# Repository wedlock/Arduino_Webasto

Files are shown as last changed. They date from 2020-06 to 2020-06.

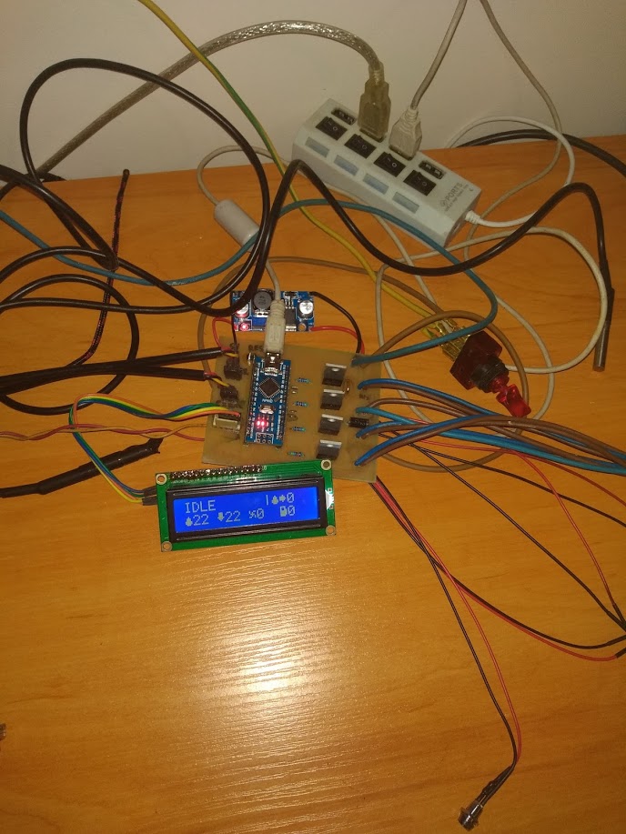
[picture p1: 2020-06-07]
IMG_20200114_202123214.jpg

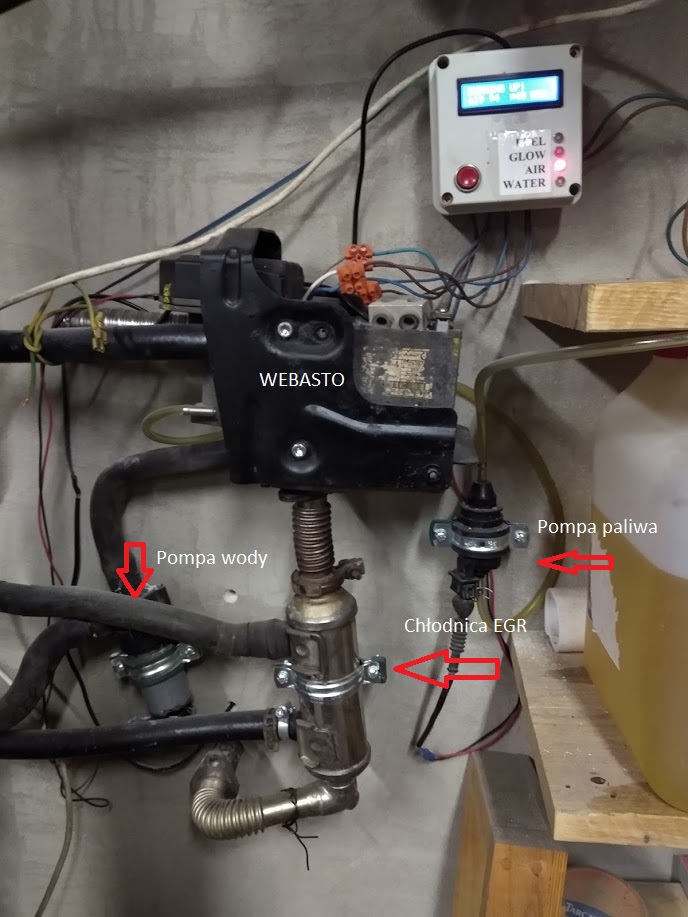
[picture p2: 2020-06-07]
IMG_20200213_185957531.jpg

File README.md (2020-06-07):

# Arduino_Webasto

Projekt sterownika do Webasto oparty na adruino ( w tym przyopadku Adruino nano ). Do działania całości niezbędne są dwa termometry ( DS18B20 ) do odczytu temperatury spalin i cieczy w układzie oraz wyświetlacz LCD 2x16 linii , 1 przycisk monostabilny, kilka rezystorów, MOSFETY i diody LED  ( wszystkie elementy są wymienione w schemacie ). Sterownik ustawiony jest na maksymalną temperaturę 70 stopni .

Do projektu dołączam pliki EAGLE i PDF niezbędne do wykonania płytki.

Krótka instrukcja działania :

Gdy sterownik znajduje się w stanie IDLE jednoktorne wciśnięcie przycisku powoduje rozpoczęcie sekwencji startowej. Na ekranie wyświetla się napis BURNING UP. Ponowne wciśnięcie przycisku w każdym momencie gdy sterownik jest w trybie BURNING UP, WORKING albo SLEEP powoduje wygaszenie pieca. Przytrzymanie przycisku 2 sek powoduje natychmiastowe zatrzymanie i reset programu.

Podczas pracy sterownik cały czas sprawdza temp. spalin i wody i gdy wykryje nieprawidłowości wyłącza układ. Mi osobiście przez całą zimę nie wyłączył się awaryjnie ani razu. Dla bezpieczeństwa wbudowałem watchdoga, który co kilka milisekund sprawdza czy arduino się zawiesiło, a jeśli tak to resetuje cału układ i wygasza się on bezpiecznie.

Stany sterownika:
1. IDLE oczekuje na włączenie ( sprawdzanie temp. cieczy ciągle włączone i ewentualnie włączy się pompa wody gdy temperatura wzrośnie )
2. BURNING UP rozpalanie pieca. Odbywa się to etapami :
  - przedmuchanie komory spalania celem pozbycia się oparów ropy
  - którkie pomowanie paliwa żeby rozsączyło się na palniku i odczekanie kulku sekund
  - włączenie świecy żarowej
  - gdy nastąpi wzrost temp. wody o 3 stopnie lub temp. wody o 2 stopnie piec przechodzi w tryb działania WORK
3. WORK - normalna praca pieca. Przy temp wody 20 stopni pompa wody jest włączana na 1/2 mocy. Zapobiega to gotowaniu się wody na powierzchni webasta. Po ogrzaniu się wody do 30 stopni sterownik urychamia się na 100% mocy. Gdy temp wody dojdzie do 70 stopni piec usypia się i czeka aż woda ostygnie do 65 stopni po czym znowy się uruchamia
4. BURN OFF wygaszanmie pieca. Nie jest podawane paliwa a wiatrak zwalnia. Zapobiega to cofaniu się płomienia. Gdy temp. spalin i wody przez dłuższą chwilę nie wzrasta, piec wyłącza się.

Na płytce zapomniałem dodać pinów do wlutowania przycisku ( ups. ) ale bez problemu da się to przylutować bezpośrednio do płytki. Są to przewody sygnałowe i ich średnica może być nawet i 0,5mm

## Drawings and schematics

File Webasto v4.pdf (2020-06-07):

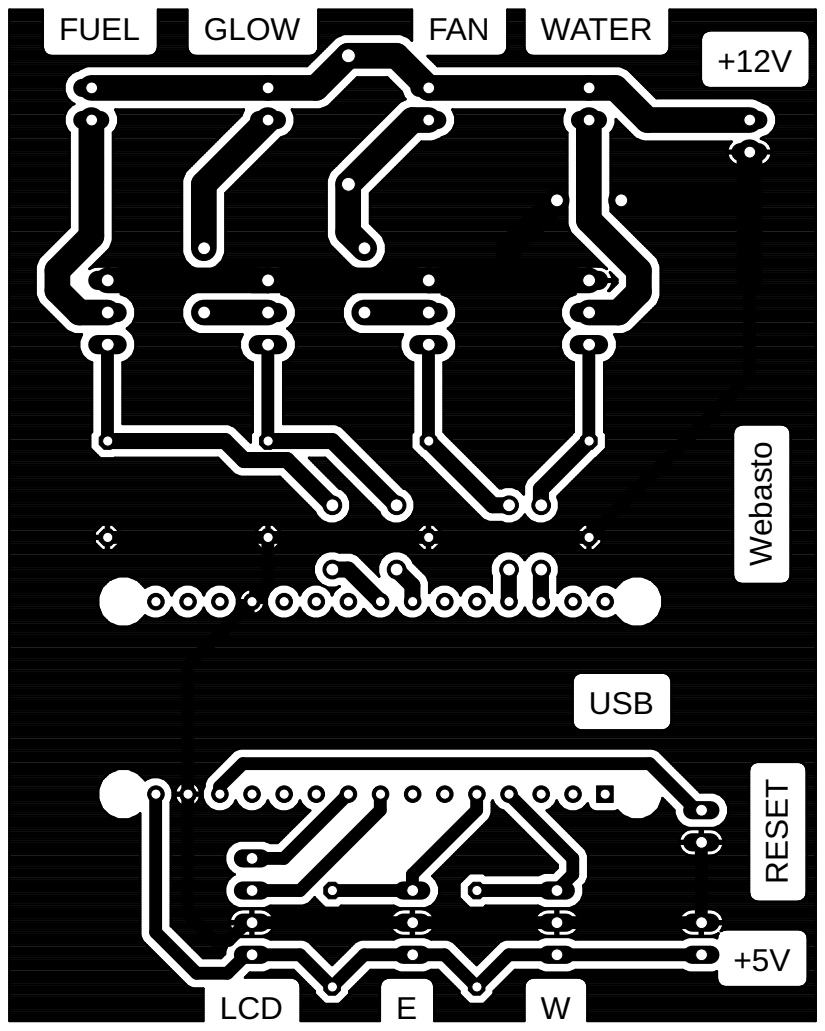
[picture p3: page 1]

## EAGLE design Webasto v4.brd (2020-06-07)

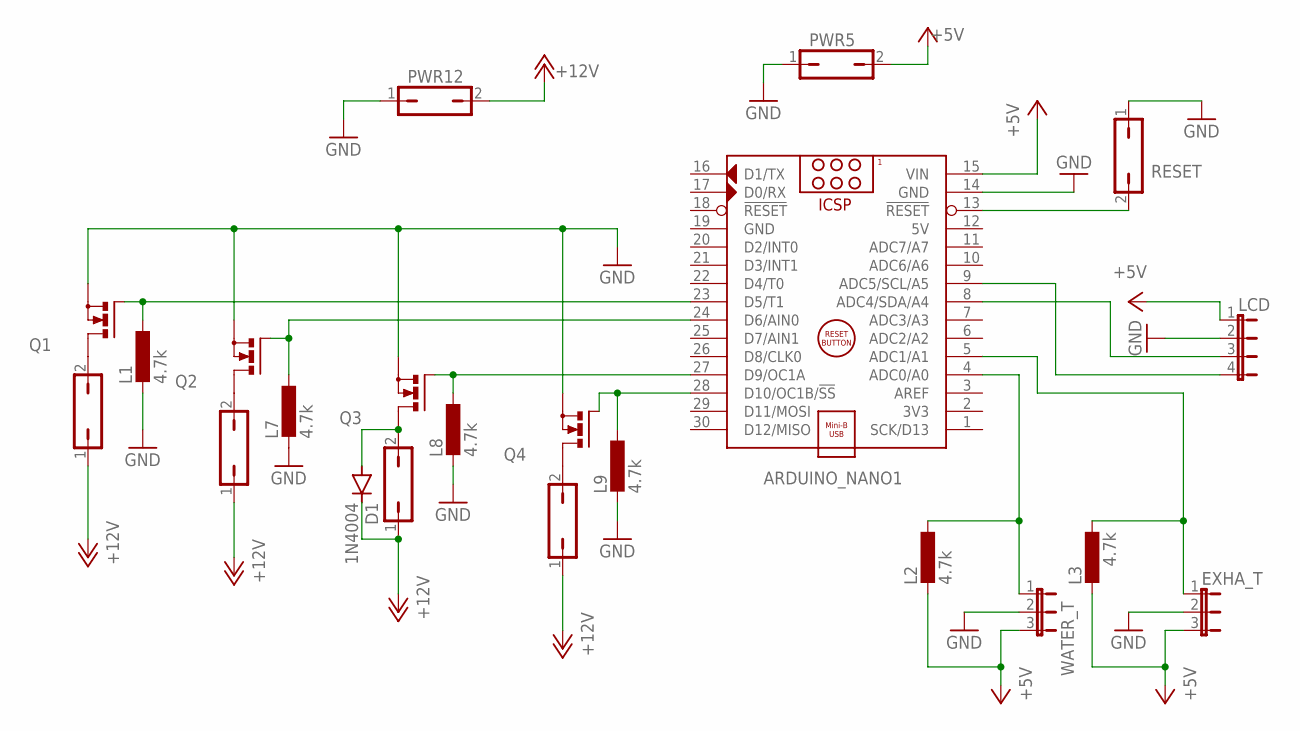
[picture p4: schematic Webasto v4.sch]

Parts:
ARDUINO_NANO1: ARDUINO_NANO
D1: 1N4004; DO41-10
EXHA_T: JP2E; JP2
FAN: 794681-2; JP1
FUEL: 794681-2; JP1
GLOW: 794681-2; JP1
L1, L2, L3, L7, L8, L9: 4.7k; 0204/7
LCD: JP4E; JP4
PWR5, PWR12: JP1Q; JP1
Q1, Q2, Q3, Q4: IRLB8721; TO220BV
RESET: power; JP1
WATER: 794681-2; JP1
WATER_T: JP2E; JP2

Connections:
5V: ARDUINO_NANO1.12 (5V)
+5V: ARDUINO_NANO1.15 (VIN), EXHA_T.3, L2.2, L3.2, LCD.1, PWR5.2, WATER_T.3
+12V: D1.C, FAN.1, FUEL.1, GLOW.1, PWR12.2, WATER.1
GND: ARDUINO_NANO1.14 (GND), ARDUINO_NANO1.19 (GND), EXHA_T.2, L1.2, L7.2, L8.2, L9.2, LCD.2, PWR5.1, PWR12.1, Q1.S, Q2.S, Q3.S, Q4.S, RESET.1, WATER_T.2
unnamed: ARDUINO_NANO1.23 (D5/T1), L1.1, Q1.G
unnamed: FUEL.2, Q1.D
unnamed: ARDUINO_NANO1.24 (D6/AIN0), L7.1, Q2.G
unnamed: GLOW.2, Q2.D
unnamed: ARDUINO_NANO1.27 (D9/OC1A), L8.1, Q3.G
unnamed: D1.A, FAN.2, Q3.D
unnamed: ARDUINO_NANO1.28 (D10/OC1B/!SS), L9.1, Q4.G
unnamed: Q4.D, WATER.2
unnamed: ARDUINO_NANO1.8 (ADC4/SDA/A4), LCD.3
unnamed: ARDUINO_NANO1.9 (ADC5/SCL/A5), LCD.4
unnamed: ARDUINO_NANO1.5 (ADC1/A1), EXHA_T.1, L3.1
unnamed: ARDUINO_NANO1.4 (ADC0/A0), L2.1, WATER_T.1
RESET: ARDUINO_NANO1.13 (!RESET), RESET.2

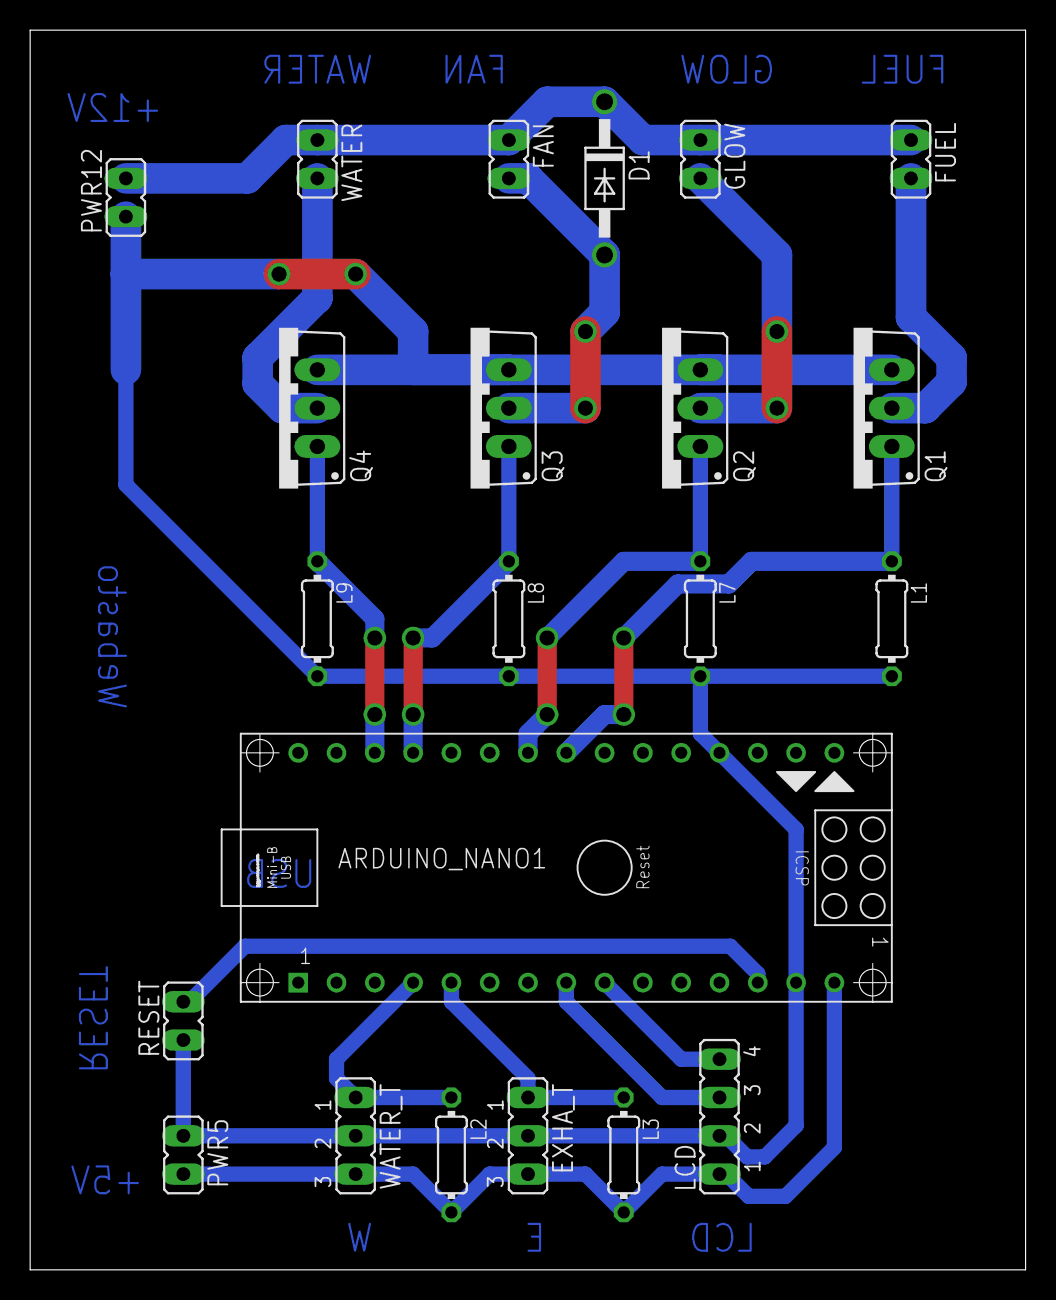
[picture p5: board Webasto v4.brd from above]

Board: 2 copper layers, 66.0 x 82.2 mm, 22 parts (0 on the bottom side), 16 nets.

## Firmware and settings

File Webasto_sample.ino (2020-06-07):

#include "Arduino.h"
#include <math.h> // needed to perform some calculations
#include <Wire.h>
#include <LiquidCrystal_I2C.h>
#include <OneWire.h>
#include <DallasTemperature.h>
#include <avr/wdt.h>

byte fanChar[ ] = {
B00000,
B10011,
B10100,
B01110,
B00101,
B11001,
B00000,
B00000 };
byte fuelChar[ ] = {
B11110,
B10010,
B10011,
B11111,
B11111,
B11111,
B11110,
B00000 };
byte waterChar[ ] = {
B00000,
B00100,
B01110,
B01110,
B11111,
B11111,
B01110,
B00000 };
byte exhaustChar[ ] = {
B01110,
B01110,
B01110,
B11111,
B01110,
B00100,
B00000,
B00000 };
byte w_pumpChar[ ] = {
B00000,
B00100,
B11110,
B11111,
B11110,
B00100,
B00000,
B00000 };

int fuel_pump_pin = 5;
int glow_plug_pin = 6;
int burn_fan_pin = 9;
int water_pump_pin = 10;
//int water_temp_pin = A0;
//int exhaust_temp_pin = A1;
int water_input_index = 0;
int exhaust_input_index = 1;
int button_pin = 3;

int temperature_target = 70;  // degres C
int run_pump_min = 30;  // minimal temperature for run water pump
int fan_speed;  // percent
int water_pump_speed;  // percent
int fuel_need;  // percent
int glow_time;  // seconds
int water_temp;  // degres C
int water_temp_sec[10];
int exhaust_temp;  // degres C
int exhaust_temp_sec[10];  // array of last 10 sec water temp, degres C
int shower_timeout;
int percent_map = 0;
int ignit_fail;
int seconds;

bool shower;
bool burn;
bool webasto_fail;
bool lean_burn;
bool overheating;
int burn_mode = 0;
bool check_pause;

int old_water_temp;
int old_exhaust_temp;
int old_fan_speed;
int old_fuel_need;
int old_fan;

int blink_LED = 13;
int blink_LED_status = 0;

LiquidCrystal_I2C lcd(0x3f, 16, 2);
DeviceAddress deviceAddress;
OneWire ds18x20[ ] = { A0, A1 };
const int oneWireCount = sizeof(ds18x20) / sizeof(OneWire);
DallasTemperature sensor[oneWireCount];

void setup() {
	webasto_fail = false;
	for (int i = 0; i < oneWireCount; i++) {
		sensor[i].setOneWire(&ds18x20[i]);
		sensor[i].begin();
		if (sensor[i].getAddress(deviceAddress, 0))
		    sensor[i].setResolution(deviceAddress, 9);
	}

//	lcd.createChar(0, waterChar);
//	lcd.createChar(1, exhaustChar);
//	lcd.createChar(2, fanChar);
//	lcd.createChar(3, fuelChar);
//	lcd.createChar(3, w_pumpChar);

	TCCR1B = (TCCR1B & 0b11111000) | 0x01;  // magic Fast PWM parameter

	pinMode(glow_plug_pin, OUTPUT);
	pinMode(fuel_pump_pin, OUTPUT);
	pinMode(burn_fan_pin, OUTPUT);
	pinMode(water_pump_pin, OUTPUT);
//	pinMode(water_temp_pin, INPUT);
//	pinMode(exhaust_temp_pin, INPUT);
	pinMode(button_pin, INPUT_PULLUP);  // important, this pulls de button pin to high, so when pressed it goes to low
	pinMode(blink_LED, OUTPUT);

	lcd.init();

	lcd.home();

	lcd.setCursor(0, 0);

	lcd.backlight();
	lcd.createChar(0, waterChar);
	lcd.createChar(1, exhaustChar);
	lcd.createChar(2, fanChar);
	lcd.createChar(3, fuelChar);
	lcd.createChar(4, w_pumpChar);

	check_pause = false;
	overheating = false;

	Serial.begin(9600);
}

void temp_data() {  // keeps the temp variables updated
	static unsigned long timer;
//	if (millis() < timer) {
//		timer = millis();
//	}
// call the get_temp function and smoothen the result
//	water_temp = (9 * water_temp + get_temp(water_temp_pin)) / 10;
//	exhaust_temp = (9 * exhaust_temp + get_temp(exhaust_temp_pin)) / 10;
	water_temp = get_temp(water_input_index);
	exhaust_temp = get_temp(exhaust_input_index);

	if (millis() > timer + 1000) {  // every sec
		timer = millis();

		for (int i = 9; i >= 1; i--) {  // updating the exhaust temperature history
			exhaust_temp_sec[i] = exhaust_temp_sec[i - 1];
			water_temp_sec[i] = water_temp_sec[i - 1];
		}
		exhaust_temp_sec[0] = exhaust_temp;  // add new temp value
		water_temp_sec[0] = water_temp;
	}
}

void control() {
	static unsigned long timer;
	if (millis() < timer) {
		timer = millis();
	}
	static bool pushed;
	static bool long_press;
	bool push;

	if (digitalRead(button_pin)) {
		push = true;
	} else {
		push = false;
	}

	if (!push && !pushed) {
		timer = millis();

	}

	if (push && !pushed) {
		timer = millis();
		pushed = true;
	}

	if (push && pushed && millis() > timer + 500) {
		if (!long_press) {  // when long press
			long_press = true;
			if (webasto_fail) {  // reset webasto fail if there has been a failure
				lcd.setCursor(0, 0);
				lcd.print("RESET     |");
				shower_timeout = 0;
				burn_mode = 0;
				burn = 0;
				glow_time = 0;
				shower = false;
				webasto_fail = false;
				check_pause = false;
				overheating = false;
			}
			if (!webasto_fail && burn_mode > 0) {  // fast stop
				lcd.setCursor(0, 0);
				lcd.print("FAST STOP |");
				burn_mode = 0;
				shower_timeout = 0;
				webasto_fail = false;
				shower = false;
				burn_mode = 0;
				burn = 0;
				glow_time = 0;
				check_pause = false;
				overheating = false;
			}
		}
	}

	if (pushed && !push) {  // if shower is off, turn it on with a 60 seconds timeout
		if (millis() > timer + 50 && !long_press) {  // when short press
			if (burn_mode > 0) {  // if shower is on, turn it off with a 15 second timeout
				lcd.setCursor(0, 0);
				lcd.print("TURN OFF  |");
				shower_timeout = 15;
				shower = false;
				burn_mode = 3;
				burn = 0;
				glow_time = 0;
				seconds = 0;
				check_pause = false;
				overheating = false;
			}
			if (burn_mode == 0) {
				lcd.setCursor(0, 0);
				lcd.print("START     |");
				shower = 1;
				shower_timeout = 99;
				check_pause = false;
				overheating = false;
			}
		}
		pushed = 0;
		long_press = 0;
	}
}

void shower_void() {

	static unsigned long secs_timer;
	if (millis() < secs_timer) {
		secs_timer = millis();
	}

	if (shower) {
		burn = 1;
		if (shower_timeout == 99) {
			shower_timeout = 60;
		}
		if (shower_timeout < 15) {  // helps to burn all the remaining fuel in the combustion chamber
			lean_burn = 1;
		} else {
			lean_burn = 0;
		}

	}

	else {  // reinitialize variables
		burn = 0;
		//seconds = 0;
		shower_timeout = 0;
		lean_burn = 0;
	}

	water_pump();  // calls the water_pump function
}

void printData(int time) {

	Serial.println(
	        "fail|igniF|shower|burn|b_mode|waterT |exhaustT|fanSpeed|fuel  |glowTime|Pump |Time");
	Serial.print("  ");
	Serial.print(webasto_fail);
	Serial.print(" | ");
	Serial.print(ignit_fail);
	Serial.print("   | ");
	Serial.print(shower);
	Serial.print("    | ");
	Serial.print(burn);
	Serial.print("  | ");
	Serial.print(burn_mode);
	Serial.print("    | ");
	Serial.print(water_temp);
	Serial.print(" | ");
	Serial.print(exhaust_temp);
	Serial.print("  | ");
	Serial.print(fan_speed);
	Serial.print("  | ");
	Serial.print(fuel_need);
	Serial.print(" |    ");
	Serial.print(glow_time);
	Serial.print("   | ");
	Serial.print(water_pump_speed);
	Serial.print("   | ");
	Serial.print(time);
	Serial.println();
}

void printLCD() {

	if (water_temp != old_water_temp) {
		lcd.setCursor(1, 1);
		lcd.print("   ");
	}
	if (exhaust_temp != old_exhaust_temp) {
		lcd.setCursor(5, 1);
		lcd.print("   ");
	}

	if (fan_speed != old_fan_speed) {
		lcd.setCursor(9, 1);
		lcd.print("   ");
	}
	if (fuel_need != old_fuel_need) {
		lcd.setCursor(13, 1);
		lcd.print("   ");
	}

	lcd.setCursor(0, 1);
	lcd.write(0);
	lcd.print(water_temp);

	lcd.setCursor(4, 1);
	lcd.write(1);
	lcd.print(exhaust_temp);

	lcd.setCursor(8, 1);
	lcd.write(2);
	lcd.print(fan_speed);

	lcd.setCursor(12, 1);
	lcd.write(3);
	lcd.print(fuel_need);

	lcd.setCursor(11, 0);
	if (check_pause) {
		lcd.print(21 - seconds);
		lcd.print(" ");
	} else {
		lcd.print("   ");
	}

//	lcd.write(0);
//	lcd.write(4);
//	lcd.print(seconds);
//	lcd.print("  ");

	if (webasto_fail) {
		lcd.setCursor(0, 0);
		lcd.print("FAIL FAIL |");
		if (blink_LED_status)
			lcd.backlight();
		else
			lcd.noBacklight();
	} else {
		lcd.backlight();
		switch (burn_mode) {
		case 0:
			lcd.setCursor(0, 0);
			lcd.print("IDLE      |");
			break;
		case 1:
			lcd.setCursor(0, 0);
			lcd.print("BURNING UP|");
			break;
		case 2:
			lcd.setCursor(0, 0);
			if (overheating)
				lcd.print("SLEEPING  |");
			else
				lcd.print("WORKING   |");
			break;
		case 3:
			lcd.setCursor(0, 0);
			lcd.print("BURN OFF  |");
			break;
		}
	}

	old_water_temp = (int) water_temp;
	old_exhaust_temp = (int) exhaust_temp;
	old_fan_speed = (int) fan_speed;
	old_fuel_need = (int) fuel_need;
}

void webasto_power() {  //calculate webasto power and set fan and fuel
	old_fan = fan_speed;
//	fan_speed = 100 - mapf(water_temp, 40, temperature_target + 10, 30, 80);  //water_temp,min water, max water, min fan, max fan
//	fuel_need = constrain(fan_speed + 20, 30, 80);
//	fan_speed = constrain(fan_speed + 10, 30, 80);

	fan_speed = 80;
	fuel_need = 50;

	if (water_temp < 30) {
		fan_speed = 60;
		fuel_need = 30;
	}

	if (water_temp > 60) {
		fan_speed = 70;
		fuel_need = 40;
	}

	if (water_temp > 65) {
		fan_speed = 60;
		fuel_need = 30;
	}

	if (old_fan != fan_speed) {
		seconds = 0;
		check_pause = true;
	}

}

void webasto() {  // this will handle the combustion
	static unsigned long timer;
	if (millis() < timer) {
		timer = millis();
	}
	static float temp_init_exhaust;
	static float temp_init_water;
	static int ignit_fail;

	if (millis() > timer + 1000) {  // every seconds, run this
		timer = millis();
		seconds++;  // increment the seconds counter
		//printData(seconds);
		printLCD();
		blink_LED_status = !blink_LED_status;
		digitalWrite(blink_LED, blink_LED_status);

	}

	if (!webasto_fail) {  // if everything's going fine

		if ((burn_mode == 0 || burn_mode == 3) && burn) {  // if the user wants a shower
			// initiate the start sequence
			burn_mode = 1;
			seconds = 0;
			temp_init_exhaust = exhaust_temp;// store the exhaust temperature before trying to start the fire
			temp_init_water = water_temp;
		}

		if ((burn_mode == 1 || burn_mode == 2) && !burn) {  // if the shower has ended
			burn_mode = 3;
			seconds = 0;
			ignit_fail = 0;
		}

		if (ignit_fail > 3) {  // if there was more than 3 attempts to start fire but all failed
			webasto_fail = true;
			burn_mode = 3;
			shower = 0;
			burn = 0;
			fan_speed = 50;
			water_pump_speed = HIGH;
		}

	} else {  // if there has been a major failure, stop everything
		shower = 0;
		burn = 0;
		ignit_fail = 0;
	}

	switch (burn_mode) {
	case 0: {  // everything is turned off in this mode
		fan_speed = 0;
		fuel_need = 0;
		glow_time = 0;
		lean_burn = 0;
	}
		break;

	case 1: {  // the fire starting sequence

		if (seconds < 5) {
			fuel_need = 0;
			fan_speed = 60;  //vent a chamber
		}

		if (seconds == 6) {
			fuel_need = 90;
			fan_speed = 40;
		}

		if (seconds == 8) {
			fuel_need = 0;  // stop and wait for it to spread all over the glow plug (important)
			// don't forget that the fan is still spinning as it wasn't turned off
		}

		if (seconds == 10) {
			glow_time = 12;  // switch on the glow plug for 12 seconds so it ignites the fuel
		}

		if (seconds == 15) {
			fuel_need = 30;
		}

		if (seconds > 17) {  // the glow plug has just been turn of (7+12=19)
			fan_speed = 50;  // get some more air and restart pumping fuel slowly
			fuel_need = 30;
		}

		if (seconds > 18) {
			if (exhaust_temp - temp_init_exhaust > 3) {  // exhaust temp raised a bit meaning fire has started
				burn_mode = 2;  // go to main burning mode and initialize variables
				seconds = 0;
				glow_time = 0;
				ignit_fail = 0;
			}
			if (water_temp - temp_init_water > 2) {  // water temp raised a bit meaning fire has started
				burn_mode = 2;  // go to main burning mode and initialize variables
				seconds = 0;
				glow_time = 0;
				ignit_fail = 0;
			}

			if (seconds > 30) {
				// the fire sequence didn't work, give it an other try
				burn_mode = 0;
				ignit_fail++;
			}
		}
		break;

		case 2:
		{
			webasto_power();  //calculate and set webasto power
			if (water_temp >= temperature_target) {  //if we reach max temp. make a sleep for webasto
				overheating = true;
			}
			if (overheating && (water_temp < temperature_target - 5)) {  //if temp is lower use start sequence
				overheating = false;
				burn_mode = 1;
			}
			if (overheating) {
				fan_speed = 20;
				fuel_need = 0;
			}
			if (!check_pause) {
				if (!overheating && (exhaust_temp - exhaust_temp_sec[9]) > 10) {  // if flame died
					burn_mode = 1;
					seconds = 0;
				}
			} else {
				if (seconds > 20) {  // wait 20 sec to establish exhaust temp after we change power
					check_pause = false;
				}
			}
		}
		if (lean_burn) {  // burn the remaining fuel in the chamber
			fuel_need = 0;
			fan_speed = 50;
		}
	}
		break;

	case 3: {  // snuff out the fire, with just a little air to avoid fumes and backfire

		fan_speed = 50;
		fuel_need = 0;
		glow_time = 0;

//		if (seconds > 30) {
//			fan_speed = 100;
//		}
		if (water_temp > water_temp_sec[9]) {  // if water temp is raising, slow down the fan
			fan_speed = fan_speed - 10;
			if (fan_speed < 20) {
				fan_speed = 20;
			}
		} else {
			fan_speed = fan_speed - 10;
			if (fan_speed > 100) {
				fan_speed = 100;
			}
		}

		if (seconds > 120 && exhaust_temp < exhaust_temp_sec[9]) {
			// turn everything off if temperature is not raising
			burn_mode = 0;
		}
	}
		break;
	}

// call every output function
	fuel_pump();
	burn_fan();
	glow_plug();
}

void fuel_pump() {
	static unsigned long timer;
	if (millis() < timer) {
		timer = millis();
	}
	static bool pulsing;
	int pulse_lenght = 11;

	if (fuel_need > 0) {
		int impulse_delay = mapf(fuel_need, 1, 100, 1000, 90);

		if (pulsing == 0 && millis() > timer + impulse_delay) {
			timer = millis();
			pulsing = 1;
		}
		if (pulsing == 1 && millis() > timer + pulse_lenght) {
			timer = millis();
			pulsing = 0;
		}
	} else {
		pulsing = 0;
	}
	analogWrite(fuel_pump_pin, 255 * pulsing);
}

void burn_fan() {
// the webasto fan runs on 10v so we need to that into account : pwm average of 14v for 10v = 0.7, 255 * 0.7 = 179
	int percent_map = mapf(fan_speed, 0, 100, 0, 179);  // pwm average of 14v for 10v = 0.7, 255 * 0.7 = 179
	analogWrite(burn_fan_pin, percent_map);
}

void glow_plug() {  // just turn the plug on if glow_time > 0, and decrement glow_time every second
	static unsigned long timer;
	if (millis() < timer || glow_time == 0) {
		timer = millis();
	}

	if (millis() < timer + glow_time * 1000) {
		digitalWrite(glow_plug_pin, HIGH);
	} else {
		digitalWrite(glow_plug_pin, LOW);
		glow_time = 0;
	}
}

void water_pump() {
	water_pump_speed = LOW;

	if (water_temp > 20) {
		water_pump_speed = 100;
	}

	if (water_temp >= run_pump_min) {
		water_pump_speed = HIGH;
	}

	digitalWrite(water_pump_pin, water_pump_speed);
}

int get_temp(int index) {
	int t_temp;
	// DANGER. Dont wait for conversion makes sometimes wrong reads
	sensor[index].setWaitForConversion(false);
	sensor[index].requestTemperatures();
	sensor[index].setWaitForConversion(true);

	t_temp = sensor[index].getTempCByIndex(0);

	if (t_temp > 200 || t_temp < -100) {  //we check here a wrong read, and make a "correction"
		if (index == water_input_index) {
			t_temp = water_temp;
		} else {
			t_temp = exhaust_temp;
		}

	}

	return t_temp;

}

float mapf(float x, float in_min, float in_max, float out_min, float out_max) {
// the perfect map fonction, with constraining and float handling
	x = constrain(x, in_min, in_max);
	return (x - in_min) * (out_max - out_min) / (in_max - in_min) + out_min;
}

void loop() {  // runs over and over again, calling the functions one by one

	wdt_enable(WDTO_1S);  //watchdog
	temp_data();
	control();
	shower_void();
	webasto();
	wdt_reset();

}
